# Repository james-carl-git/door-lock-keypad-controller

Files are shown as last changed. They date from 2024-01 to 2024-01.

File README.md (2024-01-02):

# Replacement Door Lock Combo Keypad Controller
The controller on the Kwikset combo door lock to my house died so instead of buying a new one I did the sensible thing and spent hours designing my own ;)

front-lock-pcb

back-lock-pcb

lock-installed

Features (watch video)
- Low power consumption using MSP430 allow it to run on batteries for months/years
- Easy programming with button
- Combo stored in non-volatile memory so no need to re-program when swapping batteries
- Pizo speaker for audible button presses
- Components are inexpensive and easy to get
- PCB is a small simple 2 layer board I was able to assemble with a hot plate and some solder paste (I have a few spares if interested)
- Mosfet H-bridge to spin lock motor forwards and backwards

https://github.com/james-carl-git/door-lock-keypad-controller/assets/78581339/344f8aa0-f60f-4c66-a90a-e0d3cf9ee638

Notes:
- My lock multiplexes the buttons into 5 connections/wires, they are as follows (You could probably modify the code if your lock is slightly different)
-   Row combos: 1/2 and lock | 3/4 and 5/6 | 7/8 and 9/0
-   Column combos: 1/2 and 3/4 and 7/8 | 5/6 and 9/0 and lock
- I used Energia to program the MSP430, you'll want to put the MSP430 in DIP socket so you can remove it to program it. The PCB does not break out the programing pins
- You're going to want to make sure the voltage regulator(3.3v) has a low quiescent current if you expect the batteries to last
- The combo length is set to 4 in the code but this can be changed to a value up to 16
- PCB designed with EAGLE

Below are pictures of my door lock and original PCB so you can see if maybe this design would work for you. It could also be used for a custom lock project.







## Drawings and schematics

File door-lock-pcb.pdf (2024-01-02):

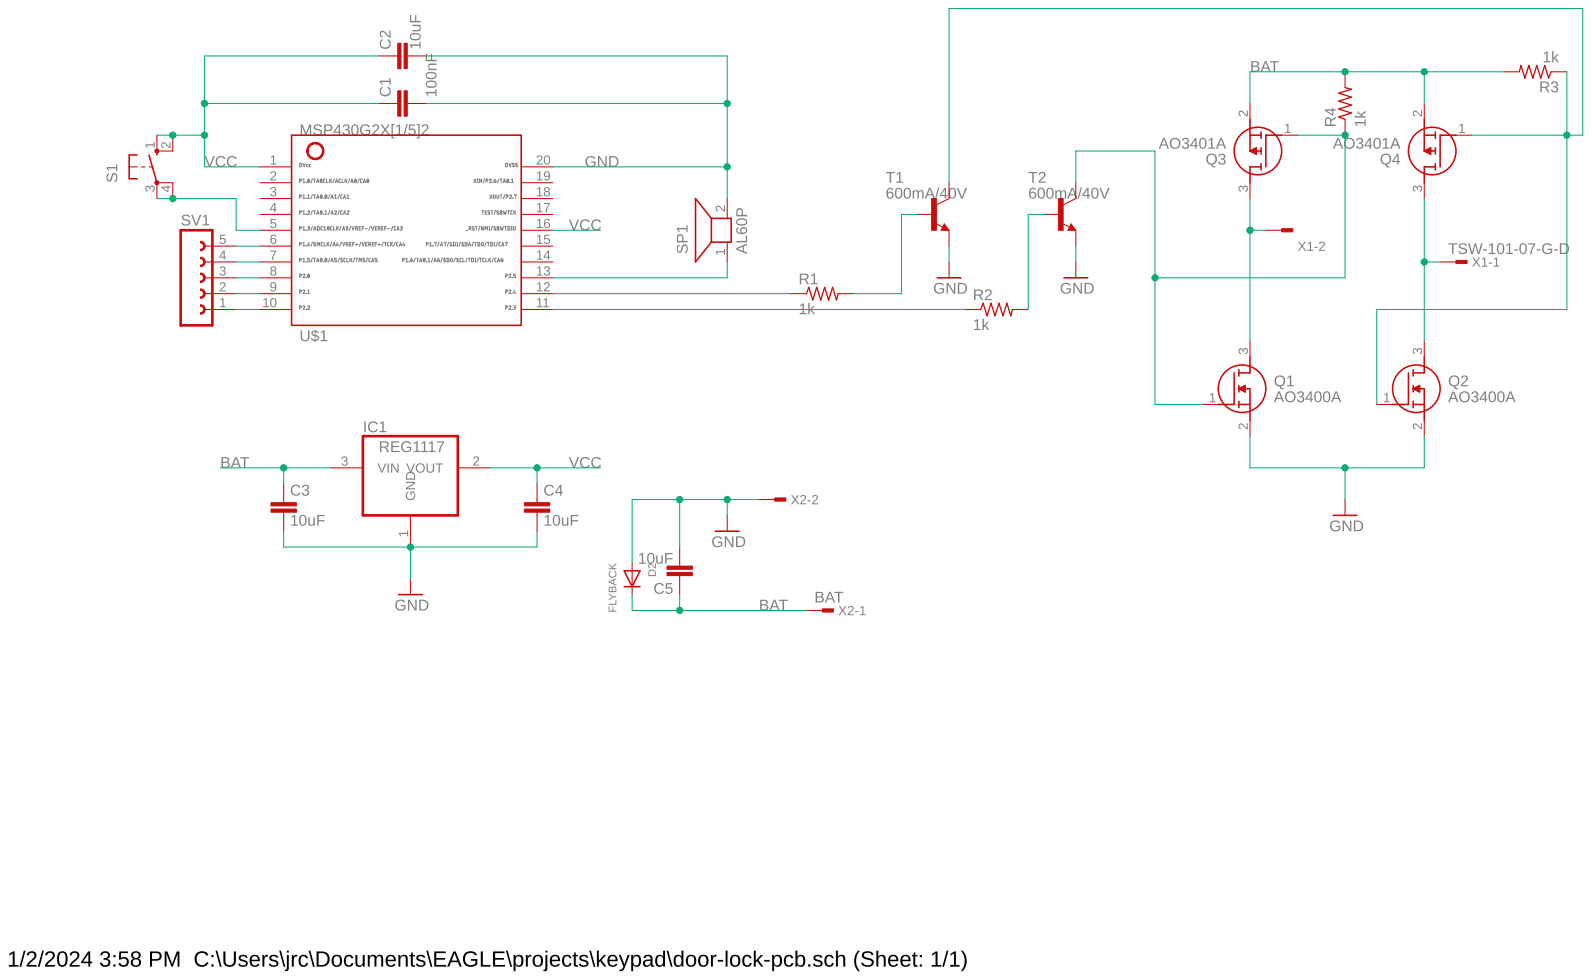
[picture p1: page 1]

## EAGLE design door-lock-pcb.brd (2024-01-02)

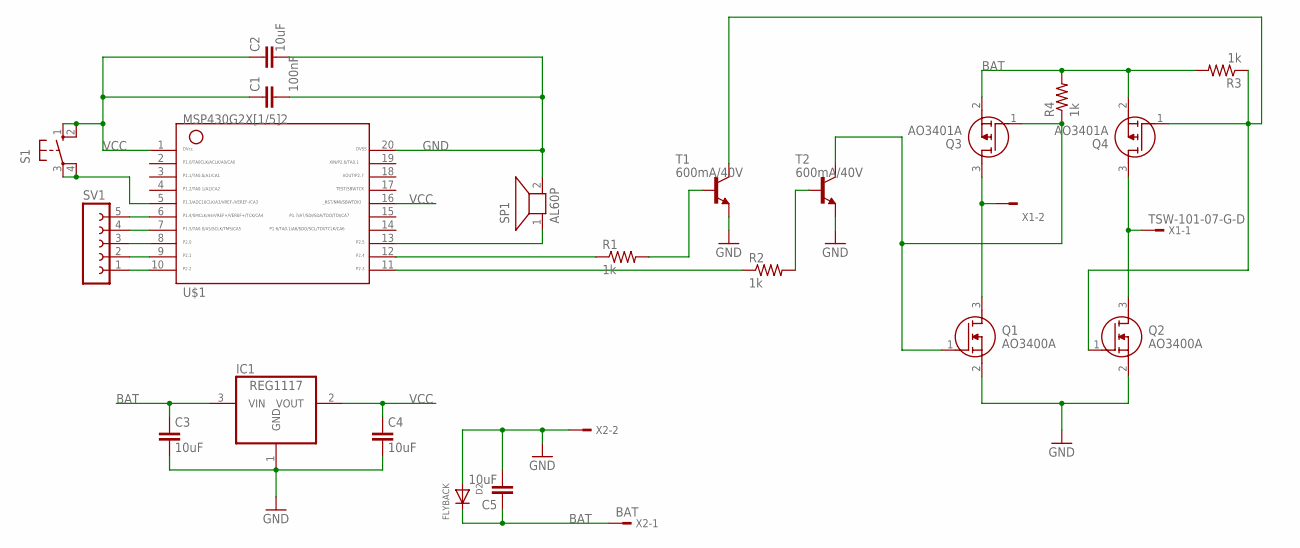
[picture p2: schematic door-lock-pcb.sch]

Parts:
C1: 100nF; CAP_0805
C2, C3, C4, C5: 10uF; CAP_0805
D2: FLYBACK; SOD-523
IC1: REG1117; SOT223
Q1, Q2: AO3400A; SOT95P280X125-3N
Q3, Q4: AO3401A; SOT95P280X125-3N
R1, R2, R3, R4: 1k; RES_0805
S1: 10-XX; B3F-10XX
SP1: AL60P
SV1: FE05-1
T1, T2: 600mA/40V; SOT23-3
U$1: G2X[1/5]2---N20; N20
X1: TSW-101-07-G-D; TSW-101-XX-G-D
X2: BAT; TSW-101-XX-G-D

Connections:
BAT: C3.1, C5.1, D2.K (C), IC1.3 (VIN), Q3.2 (S), Q4.2 (S), R3.2, R4.2, X2.1
GND: C1.2, C2.2, C3.2, C4.2, C5.2, D2.A, IC1.1 (GND), Q1.2 (S), Q2.2 (S), SP1.2, T1.2 (E), T2.2 (E), U$1.20, X2.2
unnamed: SV1.1, U$1.10
unnamed: SV1.2, U$1.9
unnamed: SV1.3, U$1.8
unnamed: SV1.4, U$1.7
unnamed: SV1.5, U$1.6
unnamed: SP1.1, U$1.13
unnamed: S1.3, S1.4 (P1), U$1.5
unnamed: Q1.1 (G), Q3.1 (G), R4.1, T2.3 (C)
unnamed: Q2.1 (G), Q4.1 (G), R3.1, T1.3 (C)
unnamed: R1.1, U$1.12
unnamed: R1.2, T1.1 (B)
unnamed: R2.2, T2.1 (B)
unnamed: R2.1, U$1.11
unnamed: Q1.3 (D), Q3.3 (D), X1.2
unnamed: Q2.3 (D), Q4.3 (D), X1.1
VCC: C1.1, C2.1, C4.1, IC1.2 (VOUT), S1.1 (S), S1.2 (S1), U$1.1, U$1.16

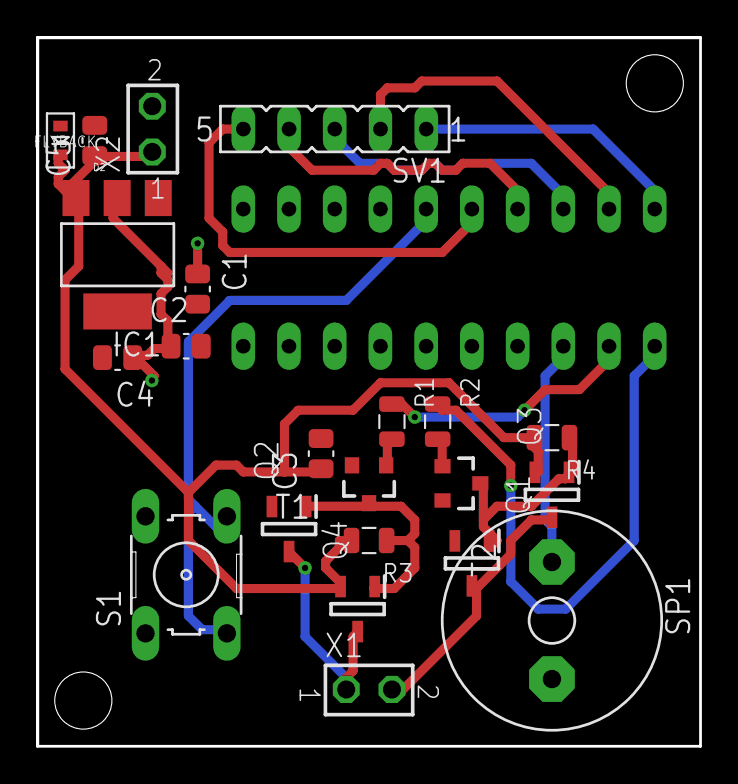
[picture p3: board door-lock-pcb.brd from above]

Board: 2 copper layers, 36.8 x 39.4 mm, 23 parts (1 on the bottom side), 18 nets.

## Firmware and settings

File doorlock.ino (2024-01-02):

/*
Replacement Door Lock Combo Keypad Controller by James Carl (@james-carl-git)
*/

#include "MspFlash.h"

#define flash SEGMENT_D

unsigned char combo[] = {0, 0, 0, 0};
unsigned char current_combo[] = {10, 10, 10, 10}; //unprogrammed default values, no combo will work
byte combo_size = 4;      //length of combo that is programmed, max 16
byte button_presses = 0;
int timeout = 0;
bool awake = false;
bool programing_mode = false;
byte correct_combos = 0;
byte lock_pin = 11;
byte unlock_pin = 12;
byte buzzer_pin = 13;
byte program_pin = 5;
byte pin_1_L = 6;
byte pin_1_3_7 = 7;
byte pin_3_5 = 8;
byte pin_5_9_L = 9;
byte pin_7_9 = 10;

// the setup routine runs once when you press reset:
void setup() {                
  // initialize pins
  pinMode(lock_pin, OUTPUT);              //lock
  pinMode(unlock_pin, OUTPUT);            //unlock
  pinMode(buzzer_pin, OUTPUT);            //buzzer
  pinMode(program_pin, INPUT_PULLDOWN);   //programming button
  pinMode(pin_1_L, INPUT_PULLDOWN);       // 1/2 - L
  pinMode(pin_1_3_7, OUTPUT);             // 1/2 - 3/4 - 7/8
  pinMode(pin_3_5, INPUT_PULLDOWN);       // 3/4 - 5/6
  pinMode(pin_5_9_L, OUTPUT);             // 5/6 - 9/0 - L
  pinMode(pin_7_9, INPUT_PULLDOWN);       // 7/8 - 9/0
  digitalWrite(pin_1_3_7, HIGH);          // need an initial state so you can detect when a button is pressed
  digitalWrite(pin_5_9_L, HIGH);
  digitalWrite(lock_pin, LOW);
  digitalWrite(unlock_pin, LOW);
  digitalWrite(buzzer_pin, LOW);
  int j = 0;
  do{                                     //read combo from flash memory and use as correct combo
    Flash.read(flash+j, &combo[j], 1);
  } while (j++ < combo_size);
}

void reset_outputs()
{
  digitalWrite(pin_1_3_7, HIGH);
  digitalWrite(pin_5_9_L, HIGH);
}

int readbutton(int button){               // determines what button is pressed and returns: 1/2=1, 3/4=3, 5/6=5, 7/8=7, 9/0=9, L=0, void=10
  if(button == 0){                        // either 1/2 or L was pressed
    digitalWrite(pin_1_3_7, LOW);    
    delay(5);
    if(digitalRead(pin_1_L)){             // L pressed
      digitalWrite(pin_1_3_7, HIGH);      // need to change state of multiplexed keypad to confirm which button was pressed
      digitalWrite(pin_5_9_L, LOW);
      if(digitalRead(pin_1_L)){           // unexpected, return void
        reset_outputs();
        return 10;
      }else{                              // Confirmed L pressed
        reset_outputs();
        return 0;
      }
    }else{                                // 1/2 pressed
      digitalWrite(pin_1_3_7, HIGH);
      digitalWrite(pin_5_9_L, LOW);
      delay(5);
      if(digitalRead(pin_1_L)){           // Confirmed 1/2 pressed
        reset_outputs();
        return 1;
      }else{                              // unexpected, return void
        reset_outputs();
        return 10;
      }
    }
  }else if(button == 1){                  // either 3/4 or 5/6 was pressed
    digitalWrite(pin_1_3_7, LOW);         // need to change state of multiplexed keypad to confirm which button was pressed
    delay(5);
    if(digitalRead(pin_3_5)){             // 5/6 pressed
      digitalWrite(pin_1_3_7, HIGH);
      digitalWrite(pin_5_9_L, LOW);
      delay(5);
      if(digitalRead(pin_3_5)){           // unexpected, return void
        reset_outputs();
        return 10;
      }else{                              // Confirmed 5/6 press
        reset_outputs();
        return 5;
      }
    }else{                                // 3/4 pressed
      digitalWrite(pin_1_3_7, HIGH);
      digitalWrite(pin_5_9_L, LOW);
      delay(5);
      if(digitalRead(pin_3_5)){           // Confirmed 3/4 pressed
        reset_outputs();
        return 3;
      }else{                              // unexpected, return void
        reset_outputs();
        return 10;
      }
    }
  }else{                                  //either 7/8 or 9/0 was pressed
    digitalWrite(pin_1_3_7, LOW);
    delay(5);
    if(digitalRead(pin_7_9)){             // 9/0 pressed
      digitalWrite(pin_1_3_7, HIGH);
      digitalWrite(pin_5_9_L, LOW);
      delay(5);
      if(digitalRead(pin_7_9)){           // unexpected, return void
        reset_outputs();
        return 10;
      }else{                              // Confirmed 9/0 press
        reset_outputs();
        return 9;
      }
    }else{                                // 7/8 pressed
      digitalWrite(pin_1_3_7, HIGH);
      digitalWrite(pin_5_9_L, LOW);
      delay(5);
      if(digitalRead(pin_7_9)){           // Confirmed 7/8 pressed
        reset_outputs();
        return 7;
      }else{                              // unexpected, return void
        reset_outputs();
        return 10;
      }
    }
  }
}

// the loop routine runs over and over again forever waiting for buttons to be pressed:
void loop() {
  int lock_or_not;
  if(digitalRead(pin_1_L)){
    awake = true;
    timeout = 0;
    lock_or_not = readbutton(0);            // check to see if either lock or 1/2 was pressed
    if(lock_or_not == 0){                   //Lock button pressed
      button_presses = 0;
      for(int k=0; k<combo_size; k++) current_combo[k] = 10;
      digitalWrite(lock_pin, HIGH);         //lock motor for 2 sec
      delay(1000);
      digitalWrite(lock_pin, LOW);
    }else{
      current_combo[button_presses] = lock_or_not;
      button_presses++;
      tone(buzzer_pin,1319);
      delay(5);
      while(digitalRead(pin_1_L))           //wait until button is released
        delay(5);
      noTone(buzzer_pin);
    }
  }else if(digitalRead(pin_3_5)){
    awake = true;
    timeout = 0;
    current_combo[button_presses] = readbutton(1);  // check to see if either 3/4 or 5/6 was pressed
    button_presses++;
    tone(buzzer_pin,1319);
    delay(5);
    while(digitalRead(pin_3_5))
      delay(5);
    noTone(buzzer_pin);
  }else if(digitalRead(pin_7_9)){
    awake = true;
    timeout = 0;
    current_combo[button_presses] = readbutton(2);  // check to see if either 7/8 or 9/0 was pressed
    button_presses++;
    tone(buzzer_pin,1319);
    delay(5);
    while(digitalRead(pin_7_9))
      delay(5);
    noTone(buzzer_pin);
  }else if(digitalRead(program_pin)){
    delay(5);
    if(digitalRead(program_pin)){
      awake = true;
      programing_mode = true;
      timeout = 0;
    }
  }
  if(awake){
    if(button_presses == combo_size){                           //have 'combo_size' presses been registered
      if(programing_mode){
        for(byte i=0; i<combo_size; i++)                        //change current combo being used in volitile memory
          combo[i] = current_combo[i];
        Flash.erase(flash);
        Flash.write(flash, current_combo, combo_size);          //write new combo to flash(non-volitile)
        delay(100);
        tone(buzzer_pin, 1568);                                 //play Tone acknowledging new combo
        delay(200);
        noTone(buzzer_pin);
        delay(200);
        tone(buzzer_pin, 1865);
        delay(200);
        noTone(buzzer_pin);
        delay(500);
      }else{
        correct_combos = 0;
        for(byte i=0; i<combo_size; i++){                     //check if entered combo matches store combo
          if(current_combo[i]==combo[i])
            correct_combos++;
        }
        if(correct_combos == combo_size){
          digitalWrite(unlock_pin, HIGH);                      //unlock motor 1 second
          delay(1000);
          digitalWrite(unlock_pin, LOW);
        }else{                                                //wrong pin, error Tone
          delay(100);
          tone(buzzer_pin, 587);
          delay(200);
          noTone(buzzer_pin);
          delay(200);
          tone(buzzer_pin, 587);
          delay(200);
          noTone(buzzer_pin);
          delay(500);
        }
      }
      correct_combos=0;
      button_presses=0;
      awake = false;
      timeout = 0; 
      programing_mode = false;
    }
    else if(timeout>1000){     //no user input, timed out (10 sec)
      correct_combos=0;
      button_presses=0;
      awake = false;
      timeout = 0;
      programing_mode = false;
    }
    else{                     //awake and waiting for another button press
      timeout++;
      delay(10);
    }  
  }
  else
    sleep(70);
}

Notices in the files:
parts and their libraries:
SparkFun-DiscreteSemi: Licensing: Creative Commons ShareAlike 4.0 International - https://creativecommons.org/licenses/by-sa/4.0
